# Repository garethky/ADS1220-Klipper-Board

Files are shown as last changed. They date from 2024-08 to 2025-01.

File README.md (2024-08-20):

# ADS1220-Klipper-Board
A board for connecting up to 4 Load cells to an ADS1220

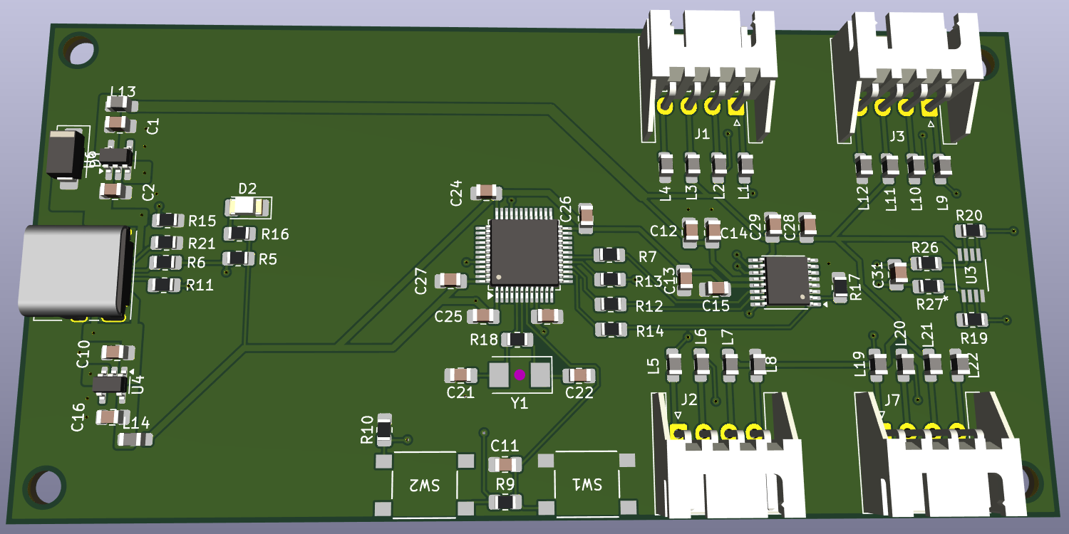
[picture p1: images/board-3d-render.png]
ADS1220 Board 3D Render


## Project Goals
This board is intended to be a reference design for eventual commercial boards that want to implement load cell probing.
We intend to tackle the following problems found with simple prototyping boards that connect via SPI I/O pins:

* Produce a clean 5V power supply on board for low noise load cell bridge measurements
* Reject common 3D printer electrical noise sources including: Voltage Regulators, Steppers, Heaters & 50Hz/60Hz line noise
* Gracefully handle Voltage Spikes & Ground Loops
* Provide Amplification/Gain to support low sensitivity (1mV/V) load cells to be able to measure 1g of force change
* Ability to connect up to 4 load cells in parallel to measure force on a printer's bed

Eventually we would like individuals to be able to order a board from a board house, once we nail down the component selection.

## Project Status: Prototyping
This is currently in the prototyping stage. Prototype goals are as follows:

1. Get it to work!
1. Prototype and test one 5V supply architecture (12V -> 5V via low noise switching regulator)
2. Test 5V to 3.3V via LDO
3. Test with and without 1 differential amplifier. 
4. Investigate voltage spikes and ground loops.

Future prototypes will refine the board:
1. Investigate additional 5V suppy architectures
2. Investigate additional amplifiers
2. Design for Supply Chain an Manufacturability: investigate component alternatives that are asier to get in the CN component supply chain.

## Specs
* ADC: [Texas Instruments ADS1220](https://www.ti.com/product/ADS1220)
* Additional differential amplifier: TK (prototype will try the [Microchip MCP6V92](https://www.microchip.com/en-us/product/mcp6v92) )
* * 4 x 4 pin JST HX connectors for full bridge load cells
* MCU: STMicro [STM32F103C8T](https://www.st.com/en/microcontrollers-microprocessors/stm32f103c8.html) MCU, Arm® Cortex® Cortex M4 @ 75Mhz
  * Klipper and Katapult support this chip well, including flashing over CAN if we decide to enable that later
* USB C for communicating with a klipper host
* Physical Boot and Reset buttons

## Why the ADS1220?
Several printers have shipped with the HX711 ADC chip which only supports 80 samples per second (SPS).
We consider this to be too slow for use as a Probe in the 3D printer as probing speed is limited to ~2mm/s.
There is a faster variant, the HX717, that supports 320 SPS. This shipped in all of Prusa's Nextuder products
and those support probing at up to 10mm/s. We consider this the minimum sample rate required for a 3D printer.

Both of these chips have the disadvantage of not being standard SPI devices and requiring a lot of MCU overhead to support communication.
Their data sheets are also lacking a lot of detail and the HX717 datasheet isnt available in English.

The ADS1220 is a good match for the capabilities of the HX717. Specifically:
* It supports faster sample rates close to 320SPS: 330, 350, 600, 660, 1000 & 1200. Higher sample rates improve the safety margin for
probing if the noise can be kept low and the sensitivity is high. Other ADC chips tend to have a large gap in the sample rate range from 
around 300SPS to 1000SPS.
* It has a PGA that supports up to a gain setting of 128
* Supports standard SPI
* TI provides a detailed datasheet and have reference designs
* Relatively cheap and widely available in the supply chain. Cost is a large
factor in getting a part into a commercial 3D printer board.

Features lacking on the ADS1220:
* The SPI speed is slow
* It lacks a "power reset" register. Reboots due to voltage spikes cant be detected at runtime.
The HX711 & HX717 also lack this feature. Higher end TI product do have this e.g. ADS1263. If we were
shipping a commercial product we would insist on this safety feature.

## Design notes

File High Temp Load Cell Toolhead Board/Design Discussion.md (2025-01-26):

## Concept
This is a 3D printer Toolead board intended to print in a "high temperature" exclosure. 80C is the target limit. This is hot for consumer pastics (Nylon, PA) but not hot for industrial plastics (PEEK & PEI - 90  to 140C). This should provide good conditions for printing the new PPA based filaments.

Because of the chamber temperature the 2 main parts that are most susceptible to heat are kept out of the chamber: the heater MOSFET and the stepper driver.

## Features

* 1 x 6 pin connector to bring in USB data, 12-24V power and your choice of fan voltage.
* 1 x 4 pin port for full bridge load cells using the ADS1220 ADC sensor
* 2 x 3 pin Fan ports with RPM monitoring (Heatbreak Cooler & Part Cooler). Max 2A power draw for the fans, limited by the input pin.
* 2 x 2 pin thermistor ports for Hot End (using PT1000 or NTC) and Heatbreak temperature monitoring
* On board NTC thermistor for board/ambient temperature monitoring
* 1 x 4 pin Neopixel/Dotstar port for illuminating the print are supplied with 5V/500mA for toolhead lighting
* On board power conversion from 12V to 5V and 3.3V using a buck converter module and two LDOs for ADC reference level DC power supply. (Does not reley on your 5V or 3.3V source being noise free)
* USB communication via wire pair in the main connector (no separate USB connector required)
* USBC Port for debugging, bench running and updates
* STM32 F103 Core M3 CPU @72Mhz
* Single wire debug (SWD) port for flashing the MCU with [Katapult](https://github.com/Arksine/katapult)
* Reset button
* MCU Boot indicator LED - also indicates USB full speed pull-up enabled
* Activity LEDs for both fans, 5V and 3.3V power
* DotStar Micro LED for indicating whatgever you want to users
* Molex CLIK-Mate connectors. Support up to 2A of current per pin and are much nicer to use vs JST alternatives.
* ESD protection (TVS diodes) on all I/O pins.
* Guard Ring for ESD protection and grounding to chassis

## References
You cant learn anything quickly without looking at the work of others. I specifically want to credit:
* [HUVUD](https://github.com/bondus/KlipperToolboard) - This is a toolhead board with an integrated stepper drive that fits on the back of a NEMA17 stepper motor. This has some incredibly tight packaging and routing in the PCB design. This particularly encouraged me to stop worrying about overlapping cortyards and just pack things closer together.
* [Prusa's Open Source](https://www.prusa3d.com/page/open-source-at-prusa-research_236812/) efforts and specifically the Love Board ([schematics](https://www.prusa3d.com/downloads/Electronics_drawings/MK4_electronics_schematics.zip)) - This is the first commercial open source board with a load cell ADC. It also pays particular attention to ESD supression and noise filtering which I found absent in other projects. The level of robustness they are achieving is worth our attention.
* The Voron project's [Klipper Expander](https://github.com/VoronDesign/Voron-Hardware/tree/master/Klipper_Expander) - this was useful for getting the Fan MOSFETs correct.
* [Tiny Fan Board](https://github.com/Gi7mo/TinyFan) - I was particularly interested in having RPM monitoring on the fan ports and this board implements that.
* Rick Heartly for this [video on grounding](https://www.youtube.com/live/ySuUZEjARPY) and PCB stackups. I'm using his preferred 4 layer stackup for this board and implementing his ideas on ground planes and via stitching.

## Detailed Design Topics
Everything, in no particular order...

### Optional USB Port
USB is used as the communications protocol. The USB D+ and D- wire pair must be twisted together to provide a good connection. A shielded twisted pair cable could also be used for these wires, so long as it can meet the requirements for continuous flexing and chamber temperatures.

I didnt see a comprelling reason to opt for CAN bus. It requires extra hardware on the host. The cable requirements for CAN are similar to USB. (remember we aret doing the super high speed version of USB)

A USBC port is included on the back side of the part and not intended to be used during normal opperation. It is included for bench running the part and performing firmware updates before it is installed into a printer. Inital flashing can be accomplished via the debug port, so this hardware isnt required. USB cabes are not rated for continous flexing conditions and high temperatures in a 3D printer. We usually build custom cables out of PTFE coated wire that can flex, resist abrasion and withstand the high temps.

The power supplied by the USB cable runs the MCU. A protection diode is incuded to stop power flowing back over the USB cable if the main power supply and the USB supple are connected at the same time. Due to voltage drop at the protection diode the 5V LDO wont see more like 4.5V and will either run in dropout mode or fail to start. If the 5V section of the board doesnt work under USB power this is OK as its just a debugging connector. If opperation is required for some test, just plug in the 24V/12V supply.

### Power
General Power Architecture:

5V USB Power |
             |
12V / 24V    --> Buck Converter --> 5.75V |--> Precision LDO --> 5V Digital
                                          |--> Precision LDO --> 5V Analog
                                          |--> Precision LDO |
3.3V Debug Power ------------------------------------------- --> 3.3V Digital

To get the most out of the ADS1220 ADC a very low noise 5V Analog reference is required. Typical LDOs are good for this but there is a more specialized class of LDO for measurment applications like this 24bit ADC. Thats what I am using here. These LDOs are voltage spcific so no external tuning resistors are required. They also have built-in reverse voltage protection so the debug port can power the board without the need for extra protection diodes.

* When using the SWD header, 3.3V power is injected directly into the 3.3V power bus
* When using the USB connector 5V power is fed into buck converter via a reverse current protection diode. The buck converter opperate din dropout mode and passes on the 5V to the LDOs. The 5V LODs will alos opperate in dropout mode.
* When bother USB and 24V are connected the protection diode stops 24V from backfeeding onto the USB power line.

#### LDO Selection

Features considered when selecting the LDO:
* Support 500mA of current output
* Fixed Voltage - eliminate external resistor netowork and saves space
* Reverse voltage protection - eliminate external diodes
* Low output voltage noise, less than 25μVRMS
* A package large enough to place by hand
* Low RθJA - Low junction-to-ambient thermal resistance

I've selected this part: TI [TPS7A21-Q1](https://www.ti.com/product/TPS7A21-Q1)

The last point about RθJA requires some math to validate. Basically this is the value that will end up limiting the current the device can supply when its inside a hot chamber at 80C.

```
SUPPLY_CURRENT = ((T(JUNCTION_MAX) – T(APPLICATION_TARGET)) / RθJA) / (V(SUPPLY) - V(OUTPUT))
```

For the TPS7A21-Q1, the T(JUNCTION_MAX) is 150°C, the RθJA of the VSON package is 58.9°C/W. The maximum input voltage to the LDO is 6V, but the target input voltage is 5.5V. Results with a value larger than the devices capacity of 500mA means there is some headroom.

```
3.3V Current @ 80°C = ((150°C - 80°C) / 58.9°C/W) / (5.5 - 3.3) = (1.19) / 2.7 = 540mA
5V Current @ 80°C   = ((150°C - 80°C) / 58.9°C/W) / (5.5 - 5.0) = (1.19) / 1.0 = 2376mA
```

If you run the calculations for a 100°C target chamber temp you still get results that are compleatly usable:

```
3.3V Current @ 100°C = ((150°C - 100°C) / 58.9°C/W) / (6.0 - 3.3) = (0.85) / 2.7 = 358mA (thermally limited!)
5V Current @ 100°C   = ((150°C - 100°C) / 58.9°C/W) / (6.0 - 5.0) = (0.85) / 1.0 = 1697mA
```

And the good news is the 5V LDO still has headroom and it is the one running the Neopixels which will pull the majority of the current from. The 3.3V rail shouldn't be pulling more than 200ma.

It is important to note that only the "DRB" 3mm x 3mm package has the good RθJA. The Specific part numbers are:

TPS7A2150PQWDRBRQ1 - 5V
TPS7A2133PQWDRBRQ1 - 3.3V

#### Buck Converter Selection
This components role is to steps down the voltage from 24V to 5.5V without generating lots of heat.

Features considered when selecting the Buck Converter:
* A Module with integrarated inductor - no hand layout required
* Support at least 1A of current output to drive both LDOs
* Support 12V-24V input voltage which are common primary supply voltages on 3D Printers
* A package large enough to hand assemble
* Low RθJA - Junction-to-ambient thermal resistance

The Buck converter is a module with a built in inductor. There is a whole art to using buck converters with external inductors. The routing of the traces can produce noise if not done correctly. A module sidesteps these concerns and reduces the complexity and part count. It just needs bulk capacitors and a resistor feedback network to opperate.

TI parts TPSM336x5 and TLVM236x5, which are the same architecture with different ranges of ouput voltage selection. Since the LDO's can accept no more than 6V, the [TLVM23615](https://www.ti.com/lit/ds/symlink/tlvm23615.pdf) is a good fit as it gives better resolution (more resistor choices) in voltage selection to 5.5V.

Thermal calculations for the buck convter are a bit different.
* T(JUNCTION_MAX) is 125°C
* Approximate efficiency is 87% or 0.87
* RθJA = 22°C/W

```
IOUT MAX = ((T(JUNCTION_MAX) – T(APPLICATION_TARGET) / RθJA) * (EFFICIENCY / 1 - EFFICIENCY) * (1 / VOUT)
```

Again, any result greater than the devices rated current of 1.5A is an indication of headroom:

```
IOUT MAX @ 80°C = ((125°C - 80°C / 22°C/W) * (0.87 / (1 - 0.87)) * (1 / 5.75) = 2.4 A
IOUT MAX @ 100°C = ((125°C - 100°C) / 22°C/W) * (0.87 / (1 - 0.87)) * (1 / 5.75) =  1.3 A (thermally limited!)
```

The module is not thermally limited at the target temp of 80C and has enough headroom to meet the applicaiton requirements at 100C.

#### Buck Converter Resistor Selection
TLVM23615 uses a resistor divider to set the output voltage between 1V and 6V. The LDO's require some margin above 5V for dropout and for voltage sags so a target of 5.5V was selected. The two resistors are called RFBB and RFBT. RFBB is typically 10kΩ and RFBT is calculated as:

RFBT kΩ = RFBB kΩ × (VOUT - 1)
RFBT kΩ = 10kΩ × (5.5 - 1) = 45kΩ

Unfortunatly, 45kΩ isn't a common size. But 45.3kΩ is. So what voltage will that yield:
45.3kΩ = 10kΩ × (VOUT - 1)
(45.3kΩ / 10kΩ) = VOUT - 1
(45.3kΩ / 10kΩ) + 1 = VOUT
VOUT = 5.53V

This is prefectly acceptable.

### PCB Stackup
The PCB stackup is: Ground/Components, Signal/Ground, Power/Signal/Ground, Ground/Components

OSH Park's 6 layer board is 'built different'. They have one large core in the middle with samller 4mil cores in between the top 3 and bottom 3 layers. This is in contrast to other stackups where its 3 double sided sheets with 2 cores.
```
1) ---Sig/PWR---
2) ---GND---
3) ---Sig/PWR---
   ===Core=== (36mil)
4) ---Sig/GND---
5) ---GND---
6) ---Sig/GND---
```
With this stackup, layers 1 and 3 reference the ground plane on 2. A signal routed on 1 and 3 doesnt require a ground return via because the ground plane doesnt change. Signals on 4 and 6 reference ground on 5. Signals moving from those layers to/from components on 1 need a ground via as a return path next to the signal via.

Because of the large core, there in minimal interaction between layers 3 and 4. But putting power on layer 4 provides a reference plane fore layer 3, in addition to the pure ground plane on layer 2.

The LDO's and Buck Converter get their best thermal performance when the board has as much copper in it as possible. Basically its a large heat spreader. Since the plan is already to pour ground everywhere this fits perfectly with what the VRMs want.

### Guard Ring
The bord is circled by a guard ring that is 2mm wide, placed on every layer of the board and stitched together with vias. The copper is exposed to allow it to be condutive. The mounting holes and mounting points on the external connectors are all tied into the guard ring.

A spot for a TVS diode to bridge the guard ring to the ground plane is provided but at the time of design its not clear if this is the right thing to do. Other options exist:
* GND and the guard ring can be connected with a large resistor.
* The guard ring can be left floating to pass ESD spikes around the board and back into the printers frame via the mounting holes.
* The load cell can be grounded to the guard ring by attacing a ring terminal to a ground wire and fixing it to the adjacent mounting point.
* The guard ring can be connected back to chassis ground via a dedicated wire back to the electronics bay. Again this can be done with ring terminals.
* ESD transmissable plastic could be used to create a cover for the board that would then be electrically connected to the guard ring.

The aim of the prototype is to test these options out in a real printer to see what performs best.

### Via Stitching
Ground planes and the Guard Ring have via stitching applied.

### ESD Protection
ESD protection, we should have some... ESD protection devices on digital lines seems to be industry standard practice and Prusa's design does this as well.

Large TVS diode between the main 24V supply and the ground plane to stop power entry ESD.

Unidirectional 3.3v TVS diodes on:
  * ADC input line for the Heatbreak Thermistor
  * ADC input lines for the Fan RPM
  * ADC input for the filament sensor (filament sesnor can be on/off or use an ADC value)

Bi-direction 3.3V TVS diodes on:
  * USB Pair

Unidirectional 5v TVS diodes on:
  * LED clock and data output line

### High Frequency Noise Filtering
Sensitive components are guarded with Ferrite beads (120R@100Mhz/3A) to filter high frequency noise.
* Load Cell lines
* Filament sensor power lines
* PT100 port lines
* Heatbreak thermistor lines
* LED power lines

### Trace Widths
The board isnt "Controlled Impedance" but I'm using the trace widths from the data table from the board house: [6 Layer impedance table](https://docs.oshpark.com/resources/six-layer-impedence-table.png).

I added the trace widths and some custom design rules to route traces by netclass at the appropriate width on outer and inner layers.

### Via Sizing
The default KiCad via size of 0.3mm / 0.6mm have an ampacity of over 2A. Thats good for basically everything on the board. The board house cant go much smaller than this anyway. In some places around the MCU i have used a smaller via size to help make space for the fanout.

### Capacitor Sizes
Capacitors de-rate at the target 80C chamber temperatures. Larger capacitors de-rate less than smaller ones. I'm also hand assembling the board and decided the smallest component I want to place manually is a 0603. This chart is used to select capacitor sizing:

| Range C | SMD Size | Type | Voltage | Range |
|---|---|---|---|---|
| 1pf - 10nf | 0603 | Ceramic C0G | 25V | 10% |
| 10nf - 0.1uf | 0603 | Ceramic X7R | 25V | 10% |
| 0.1uf - 2.2uF | 0805 | Ceramic X7R | 25V | 10% |
| 2.2uF - 22uF | 1206 | Ceramic X7R | 70V | 10% |

Nothing in the design requires an electrolytic capacitor.

### LEDs
Leds are driven by 24V, 5V and 3.3V power. Resistors are selected to limit the LED's driven current to about than 2ma. 3.3V output pins on the MCU supply a maximum of 25mA of current.

[LIST-C193KRKT-5A - LiteOn](https://optoelectronics.liteon.com/upload/download/DS22-2005-077/LTST-C193KRKT-5A.PDF)
Forward Voltage: 2.0V
Forward Current: 1.5mA

| LED Module | Supply Voltage | Resistor | Current | Forward Voltage (FV) |
|---|---|---|---|---|
| LIST-C193KRKT-5A | 24V  | 10KΩ | 2.2mA | 2.0v |
| LIST-C193KRKT-5A | 5V | 2kΩ | 1.5mA | 2.0v |
| LIST-C193KRKT-5A | 3.3V | 1kΩ | 1.3mA | 2.0v |

Resistors should be able to handle 1/2 watt of power or better. Usually this requires 0805 size resistors.

Some tuning of this might be required in the prototype based on brightness.

### Fans

#### Fan Voltage
A dedicated input pin allows you to pick the supply voltage for the fans. I dont have to generate 12V on board to run them.

#### Fan RPM Monitoring
My personal view is that cooling fans are safety critical systems that should be monitored. If the fan fails the printer should shut down the heater. So the fans on this board feature an RPM monitoring pin. There are plenty of fans in the supply chain that have this feature.

#### No Fan PWM Output
4 Wire fans in this size do exist but they are very rare. If you use a 4 wire fan, you dont need to put MOSFETs on the board to drive the fans. This effectivly means you can get the MOSFET into the place where its more likely to get cooled. But the lack of fans means this is very unlikely to happen, so I left this out. If I had my way I would require 4 wire fans and omit the MOSFETs.

#### Tach Line Resistor
Fans report their RPM or Tachometer as a square wave. A reference voltage is supplied in to the fan's tachometer input. The fan then pulls this line low to create a square wave. This means the tach line voltage supply connects to ground inside the fan. Both [Noctua](https://noctua.at/pub/media/wysiwyg/Noctua_PWM_specifications_white_paper.pdf) and [Sunon](https://www.sunon.com/PROSEARCH_FILES/(D04115420G-01)-1.pdf) require limiting the current flowing through the tach line to not more thean 5mA. This is important to do as, when the RPM is 0, the line may be pulled low continouously causing a large current flow through the fan. All the other designs I have seen omit this resistor.

E.g. the [Tiny Fan Board](https://github.com/Gi7mo/TinyFan) uses an in-mcu pull-up on the ADC line and connects it directly to the Tachometer input. The Pins on an STM32 chip can supply up to 25mA which is 5x higher than the industry spec.

```
R = V/I
R = 3.3V / 5mA
R = 660 Ohm
```

This is really close to 1k, so thats what im using as this helps with BOM consolidation.

#### Fan MOSFET Selection
Slection criteria:

* The max voltage is 24V. So at least a 30V (Drain to Source V<sub>DS</sub)) device is required.
* Duty cycle is 100% / full DC on. We do use PWM for the part cooling fan but the hot end fan is usually 100% on.
* Ambiend temp target is 80C.
* The gate drive voltage is 5.0. So V<sub>GS</sub> needs to be less than 3.3V. I'm re-using the level shifter part to step up the 3.3V GPIO voltage to 5V.
* Because of the focus on 100% duty cycle we want a very low resistance MOSFET. Leakage current isnt really an issue in this application.
* The current required is less than 1A. However it has to do this at 100% duty cycle at 80C ambient.

The last part is actually really difficult. Most data sheets show 100% duty cycle under ideal conditions, both gate drive voltage and ambient temperature. We will have neither of these conditions.

I didnt want to conduct a survey of all possible MOSFET parts, so I looked in TI's parts bin and found: [CSD17581Q3A](https://www.ti.com/lit/ds/symlink/csd17581q3a.pdf)

I increased the gate resistor value from 100 Ohms to 1K Ohms. Some designs omit this resistor, but this increases power used by the MOSFET and drives up its temperature. I'd like to have some math to work out the how fast the gate needs to switch and calulate an optimal value. Klipper's default switching time is 10ms in software PWM mode. This is 100Hz, a very slow switching speed. It is possible that higher switching speed might work for some fans when using hardware PWM.

#### Fans and N-Channel MOSFETs
An N channel mosfet switches the ground lead of the fan. This disconnects the fan from ground. This should also defeat the fans ability to pull the Tach line low, disrupting the tach signal. For a safety monitoring usecase, this is an acceptable defect. We dont need the reported RPM to be acurate.

This behaviour is something that I plan to investigate with a scope. I saw some suggestions that the ground lead should bypass the MOSFET with a high value pulldown resistor. I added these as do-not-populate parts on the board to experiment with.

### MCU Crystal

#### Why not an Oscillator Module?
I wanted to use a crystal oscillator module for this project to save on space and complexity. But I found this to be impossible with the current katapult/klipper codebase:

###### OSC_OUT Pin
This is the pin that would normally complete the crystal oscillator circuit. When using an oscillator module its less than clear what must be done from the documentation. But as best as I understand it:
* [AN1709](https://www.st.com/resource/en/application_note/an1709-emc-design-guide-for-stm8-stm32-and-legacy-mcus-stmicroelectronics.pdf) has an explicit diagram with the pin tied to ground when using an external clock source. This fits with the recommendation to tie all unued GPIO pins to GND to minimize noise.
* [AN5286](https://www.st.com/resource/en/application_note/an2586-getting-started-with-stm32f10xxx-hardware-development-stmicroelectronics.pdf) has a similar diagram (Figure 6) that shows the OSC_OUT pin unconnected with a "Hi-Z" note. Hi-Z mean high impedance. There is a "BYPASS" / `HSEBYP` mode that needs to be configured in software that disconnects the OSC_OUTPUT from the clock source. I assume this is how you set the "Hi-Z" mode for the pin.
* I'm pretty sure [this code](https://github.com/Arksine/katapult/blob/25a23cd420d7f0f7b677f1511b5739385fca72d9/lib/stm32f1/system_stm32f1xx.c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) in katapult turns off that bypass mode. This isn't user configurable, so the bypass mode is never available, meaning only crystals should be used.

Its not clear if using the module in non-bypass mode will work correctly if the pin is grounded or floating, since the bypass mode is not engaged.

#### Crystal Capacitor Selection

I selected [ECS-.327-6-34QCS-TR](https://ecsxtal.com/store/pdf/ECX-34Q.pdf) using the STM32 crystal selection tools. I wanted one that had a small footprint and a high temperature rating, this one is good to 125C.

The load capacitance of the crystal is 12.5pF. The 'back of the envelope' method for selecting a capacitor size is to double the load capacitance. So 25pF.

You can do the complete math. But STM's own document, [AN2867](https://www.st.com/resource/en/application_note/an2867-guidelines-for-oscillator-design-on-stm8afals-and-stm32-mcusmpus-stmicroelectronics.pdf), says the best thing to do is to measure the frequency generated with a scope and tune the capacitance based on those results. I'm not sure that my scope is good enough to do this.

### Unused Pins
What is the correct thing to do with unused pins?

STM have an app note [AN4899](https://www.st.com/content/ccc/resource/technical/document/application_note/group0/13/c0/f6/6c/29/3b/47/b3/DM00315319/files/DM00315319.pdf/jcr:content/translations/e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) that advises connecting all unused pins to GND: "If the application is sensitive to ESD, prefer a connection to ground".

There is however a risk specific to klipper with this. Klipper users can enable a pull-up on one of these pins by accident, creating a short to ground. This will probably cause that pin to burn out but it could do damage to other parts of the MCU in the process. The alternative is to use a resistor in the ground path to prevent this damage. This adds about 5 extra resistors around the MCU, which is space id rather not use up.

So the mitigation I have is to ship a klipper "pins file" which gives friendly names to all of the pins. This should discourage myself or someone else from doing a pull-up on the wrong pin. It also helps that NOTHING on the board requires a pull-up. All pull-ups have been done for you in hardware.

Most of the other chips have something similar in the documentation about connecting unused pins to ground.

### Test Points
Most of the items on the board can be gotten to via the rather generous pads for the connectors. Here is a list of everythign I want to scope and how im planning to get to it:

* GND - Via Connector Pad
* 3.3V - Test Point
* 5V Digital - TestPoint
* 5V Analog - TestPoint +  a local GND test point

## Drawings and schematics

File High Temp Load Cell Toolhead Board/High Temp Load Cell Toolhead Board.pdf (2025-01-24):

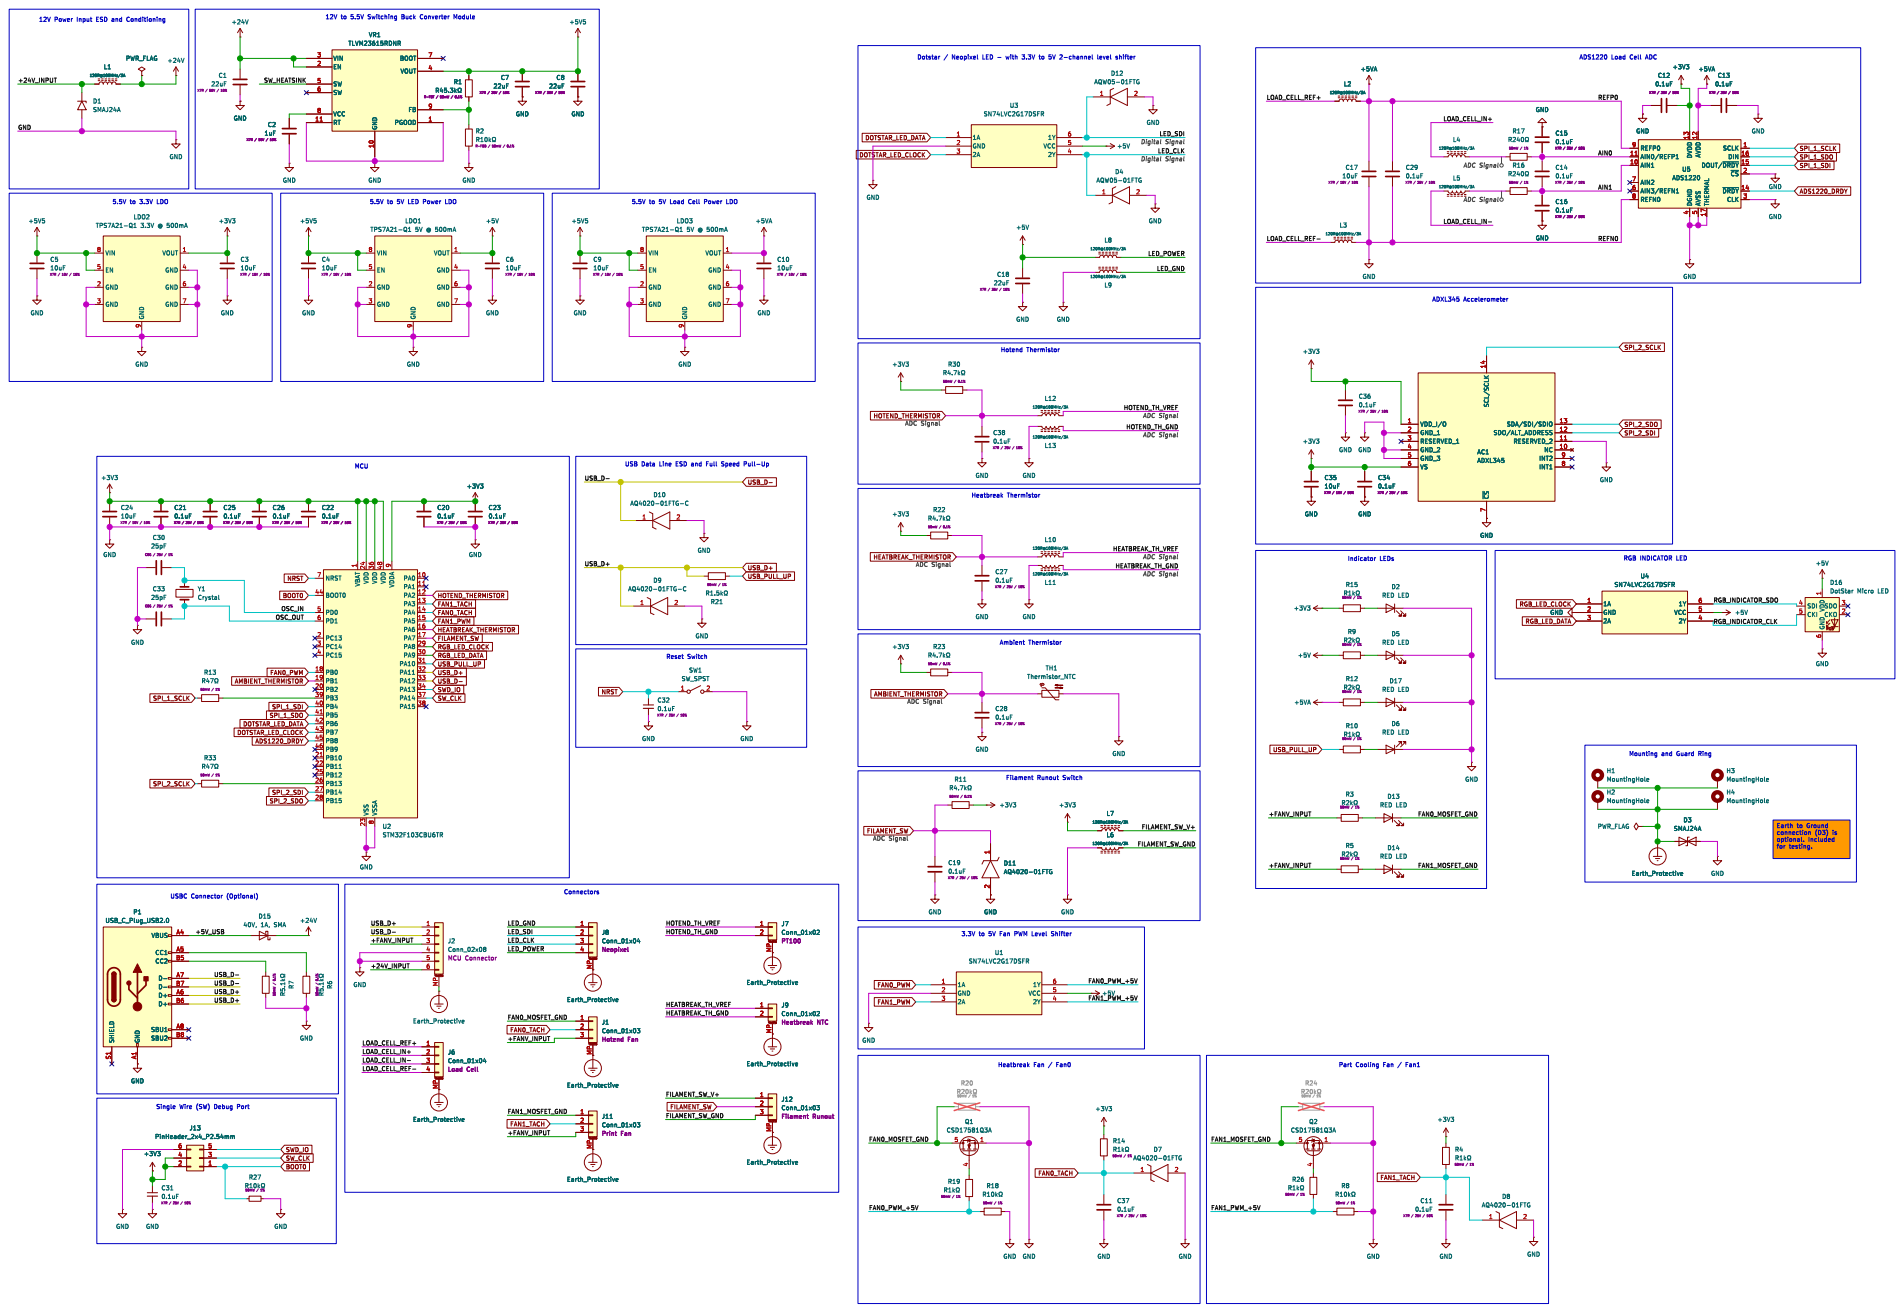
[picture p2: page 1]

12V Power Input ESD and Conditioning

16 THERMAL 17
~{DRDY} 14 DOUT/~{DRDY}15 DIN

SCLK

ADC Signal

ADXL345 Accelerometer 5.5V to 5V LED Power LDO

5.5V to 5V Load Cell Power LDO

1 PA0 10 PA1 11 PA2 12 PA3 13 PA4 14 PA5 15 PA6 16 PA7 17 PB0 18 PB1 19 PC13 2 PB2 20 PB10 21 PB11 22 VSS 23 VDD 24 PB12 25 PB13 26 PB14 27 PB15 28 PA8 29 PC14 3 PA9 30 PA10 31 PA11 32 PA12 33 PA13 34 VDD 36 PA14 37 PA15 38 PB3 39 PC15 4 PB4 40 PB5 41 PB6 42 PB7 43 BOOT0 44 PB8 45 PB9 46 VDD 48 PD0 5 PD1 6 NRST 7 VSSA

Single Wire (SW) Debug Port

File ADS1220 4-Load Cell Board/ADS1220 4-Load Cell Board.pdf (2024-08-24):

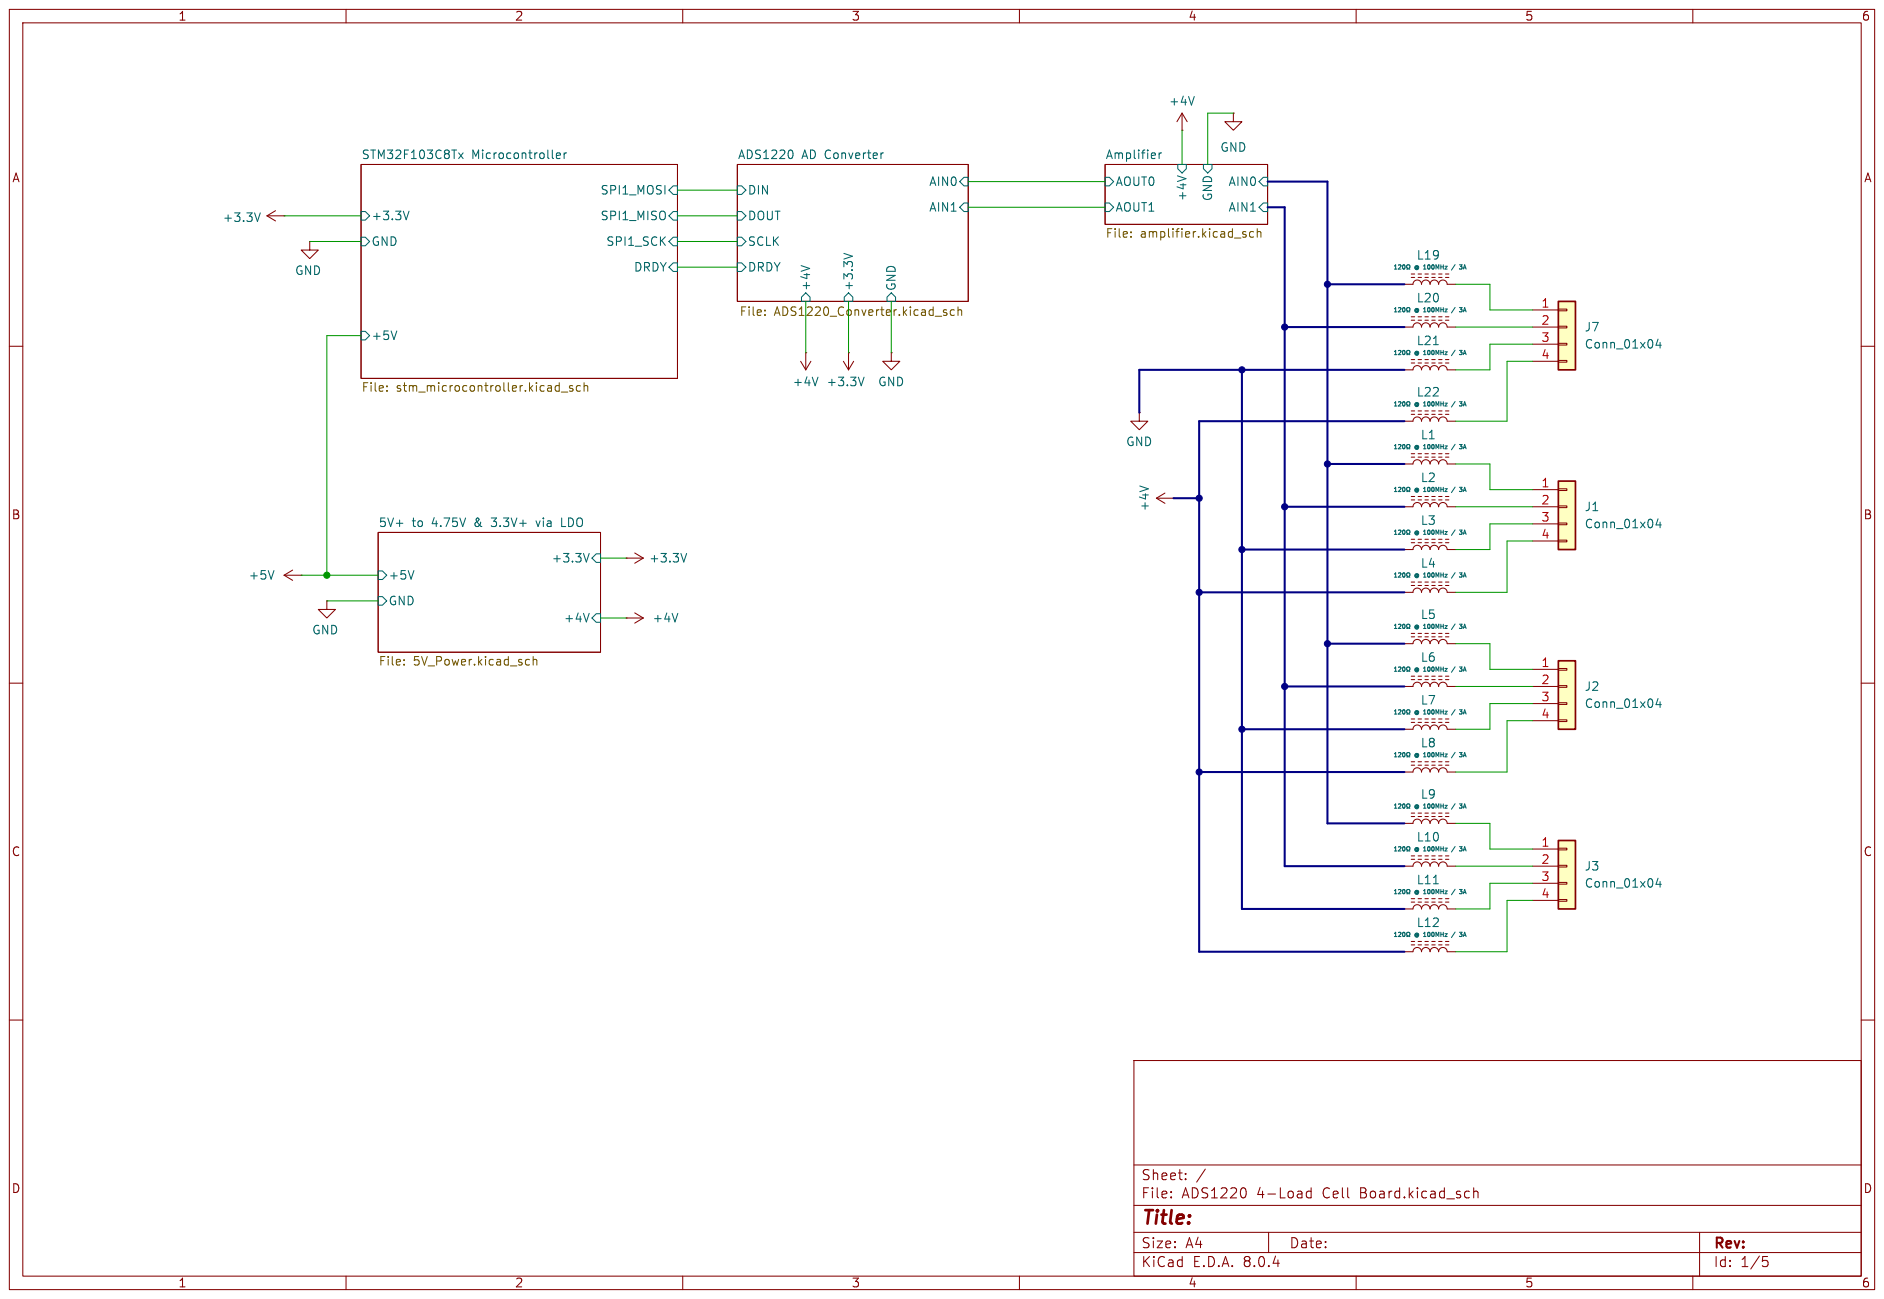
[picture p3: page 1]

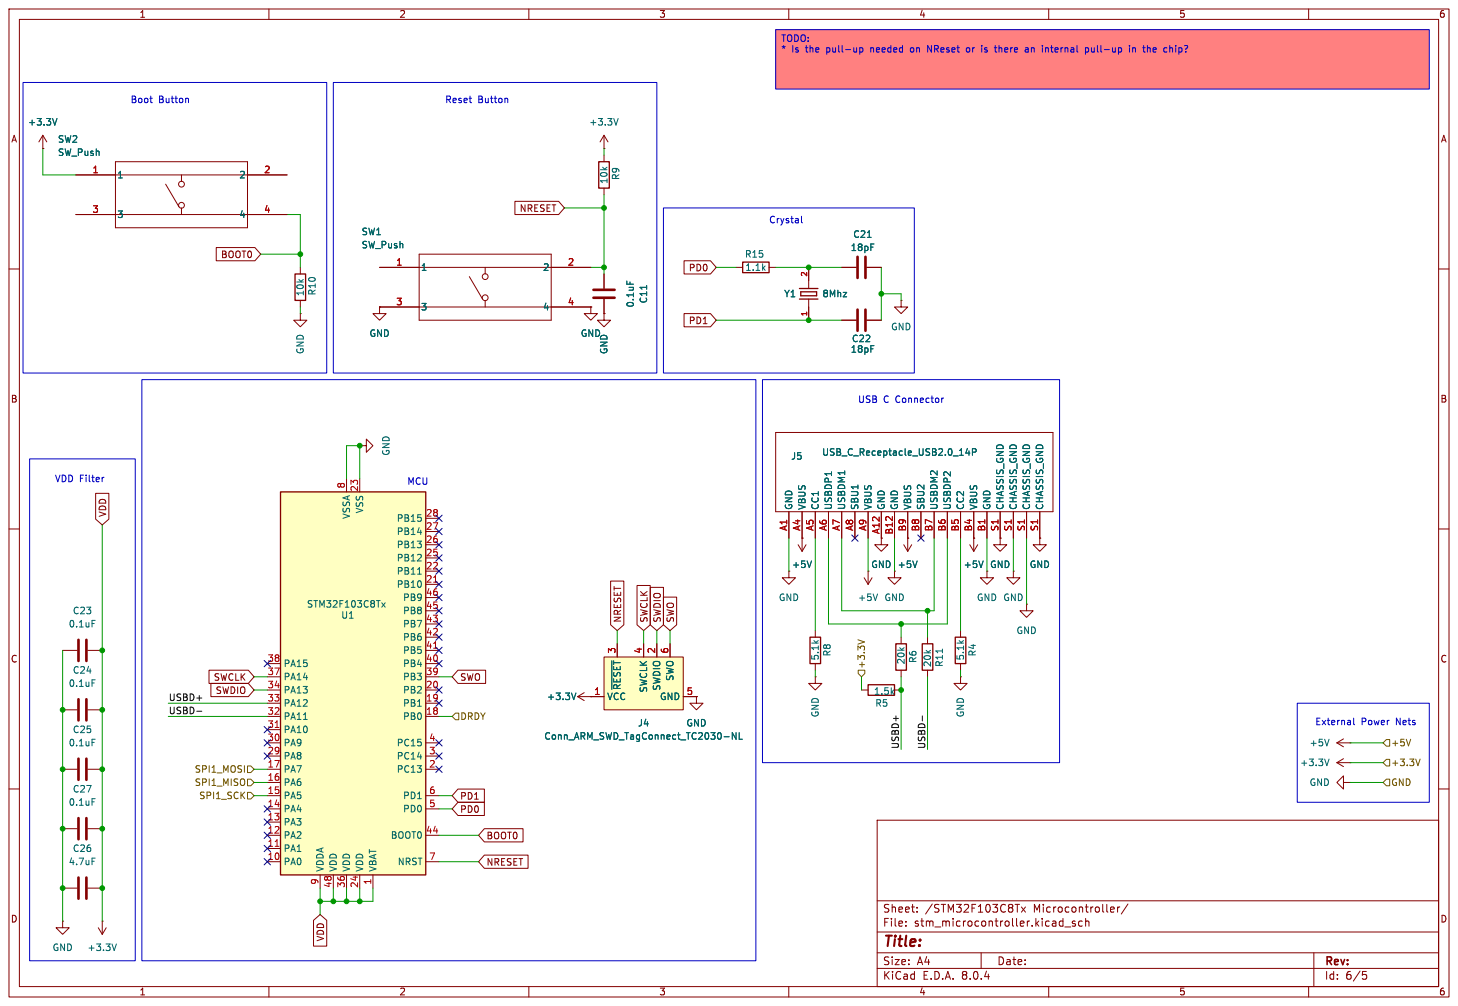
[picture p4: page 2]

1 PA0 10 PA1 11 PA2 12 PA3 13 PA4 14 PA5 15 PA6 16 PA7 17 PB0 18 PB1 19 PC13 2 PB2 20 PB10 21 PB11 22 VSS 23 VDD 24 PB12 25 PB13 26 PB14 27 PB15 28 PA8 29 PC14 3 PA9 30 PA10 31 PA11 32 PA12 33 PA13 34 VDD 36 PA14 37 PA15 38 PB3 39 PC15 4 PB4 40 PB5 41 PB6 42 PB7 43 BOOT0 44 PB8 45 PB9 46 VDD 48 PD0 5 PD1 6 NRST 7 VSSA

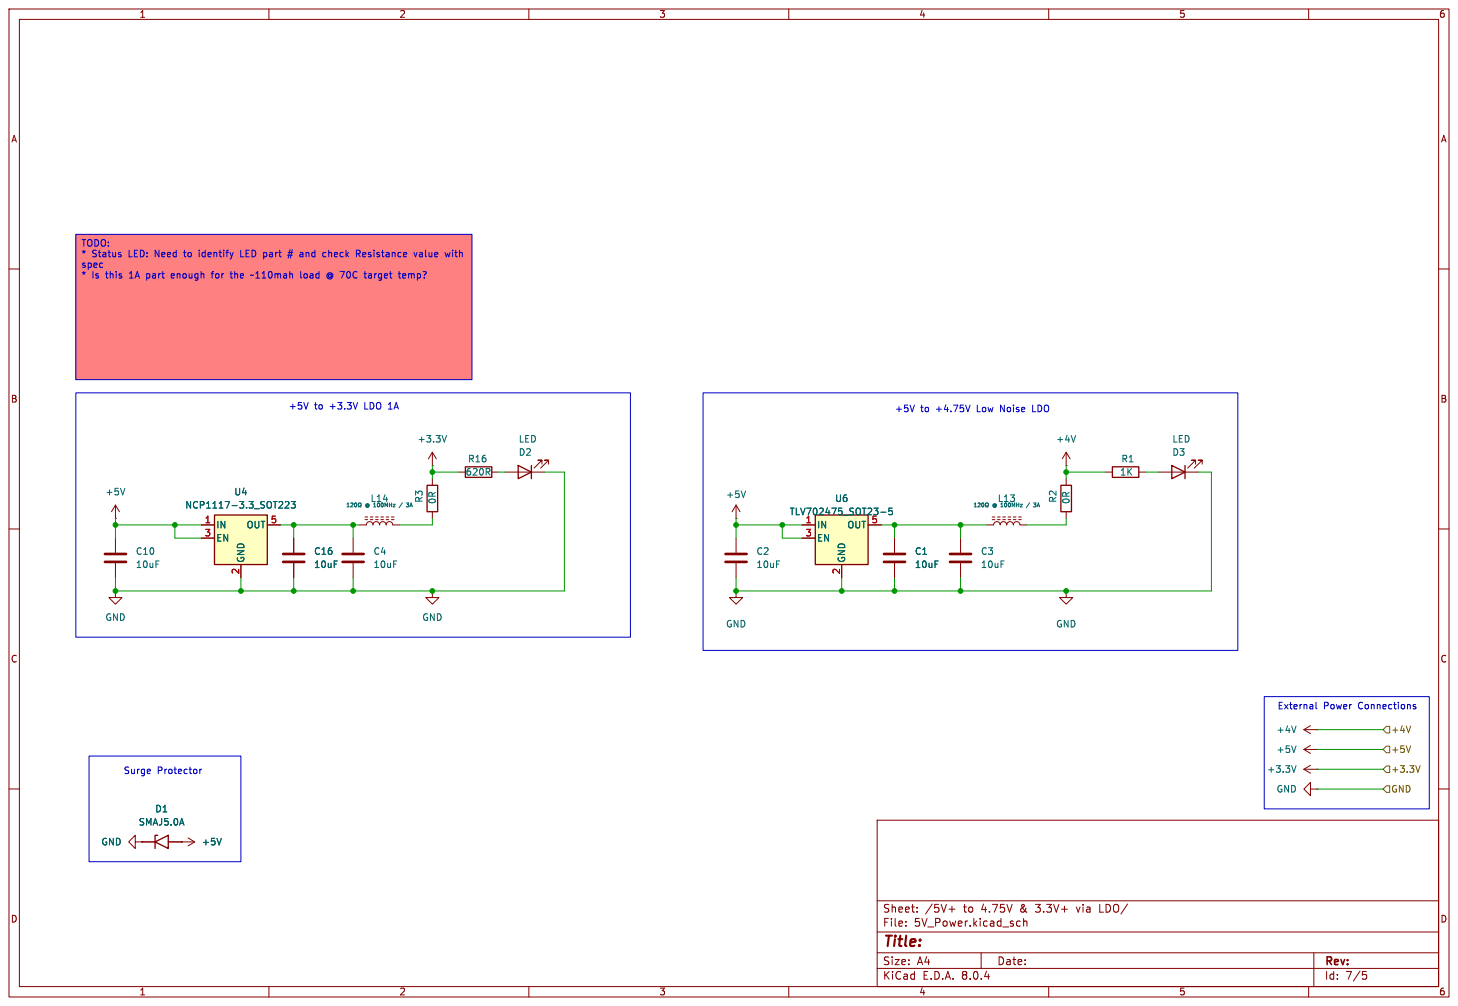
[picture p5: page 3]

spec
* Is this 1A part enough for the ~110mah load @ 70C target temp? C16

External Power Connections Surge Protector

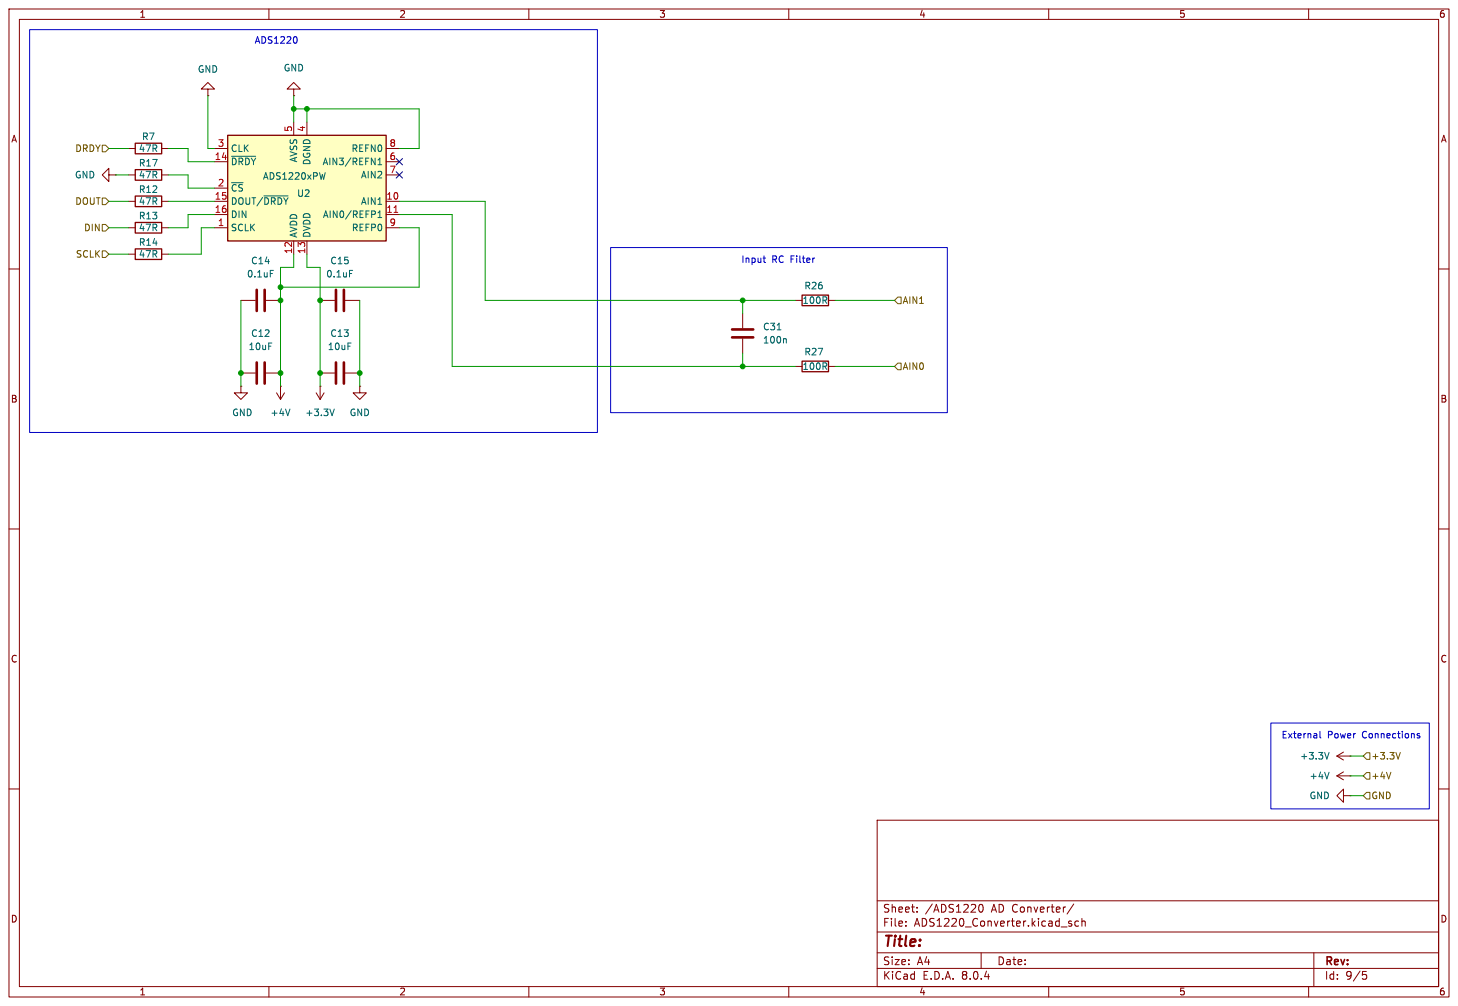
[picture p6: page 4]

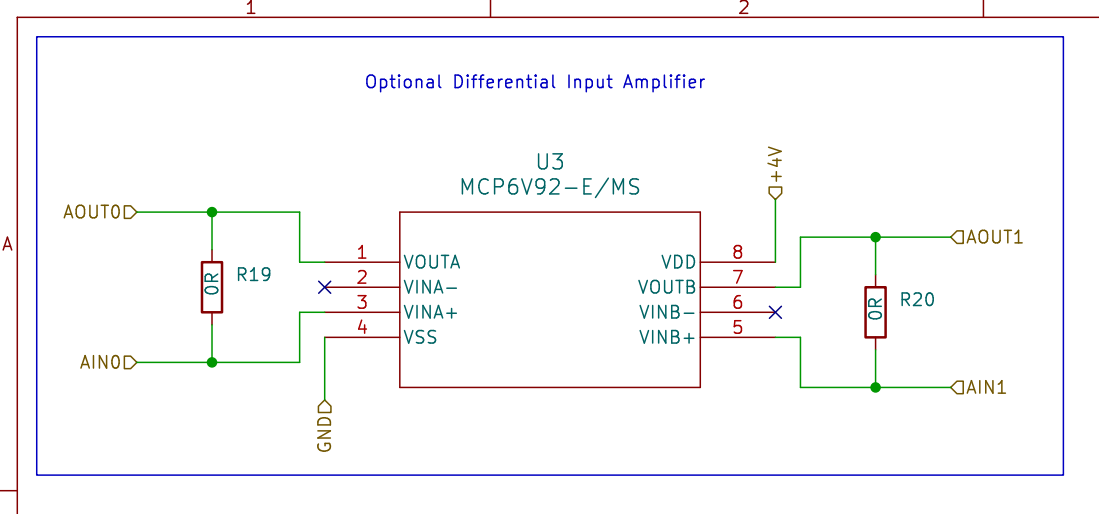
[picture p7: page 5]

Id: 10/5 Title: File: amplifier.kicad_sch Sheet: /Amplifier/

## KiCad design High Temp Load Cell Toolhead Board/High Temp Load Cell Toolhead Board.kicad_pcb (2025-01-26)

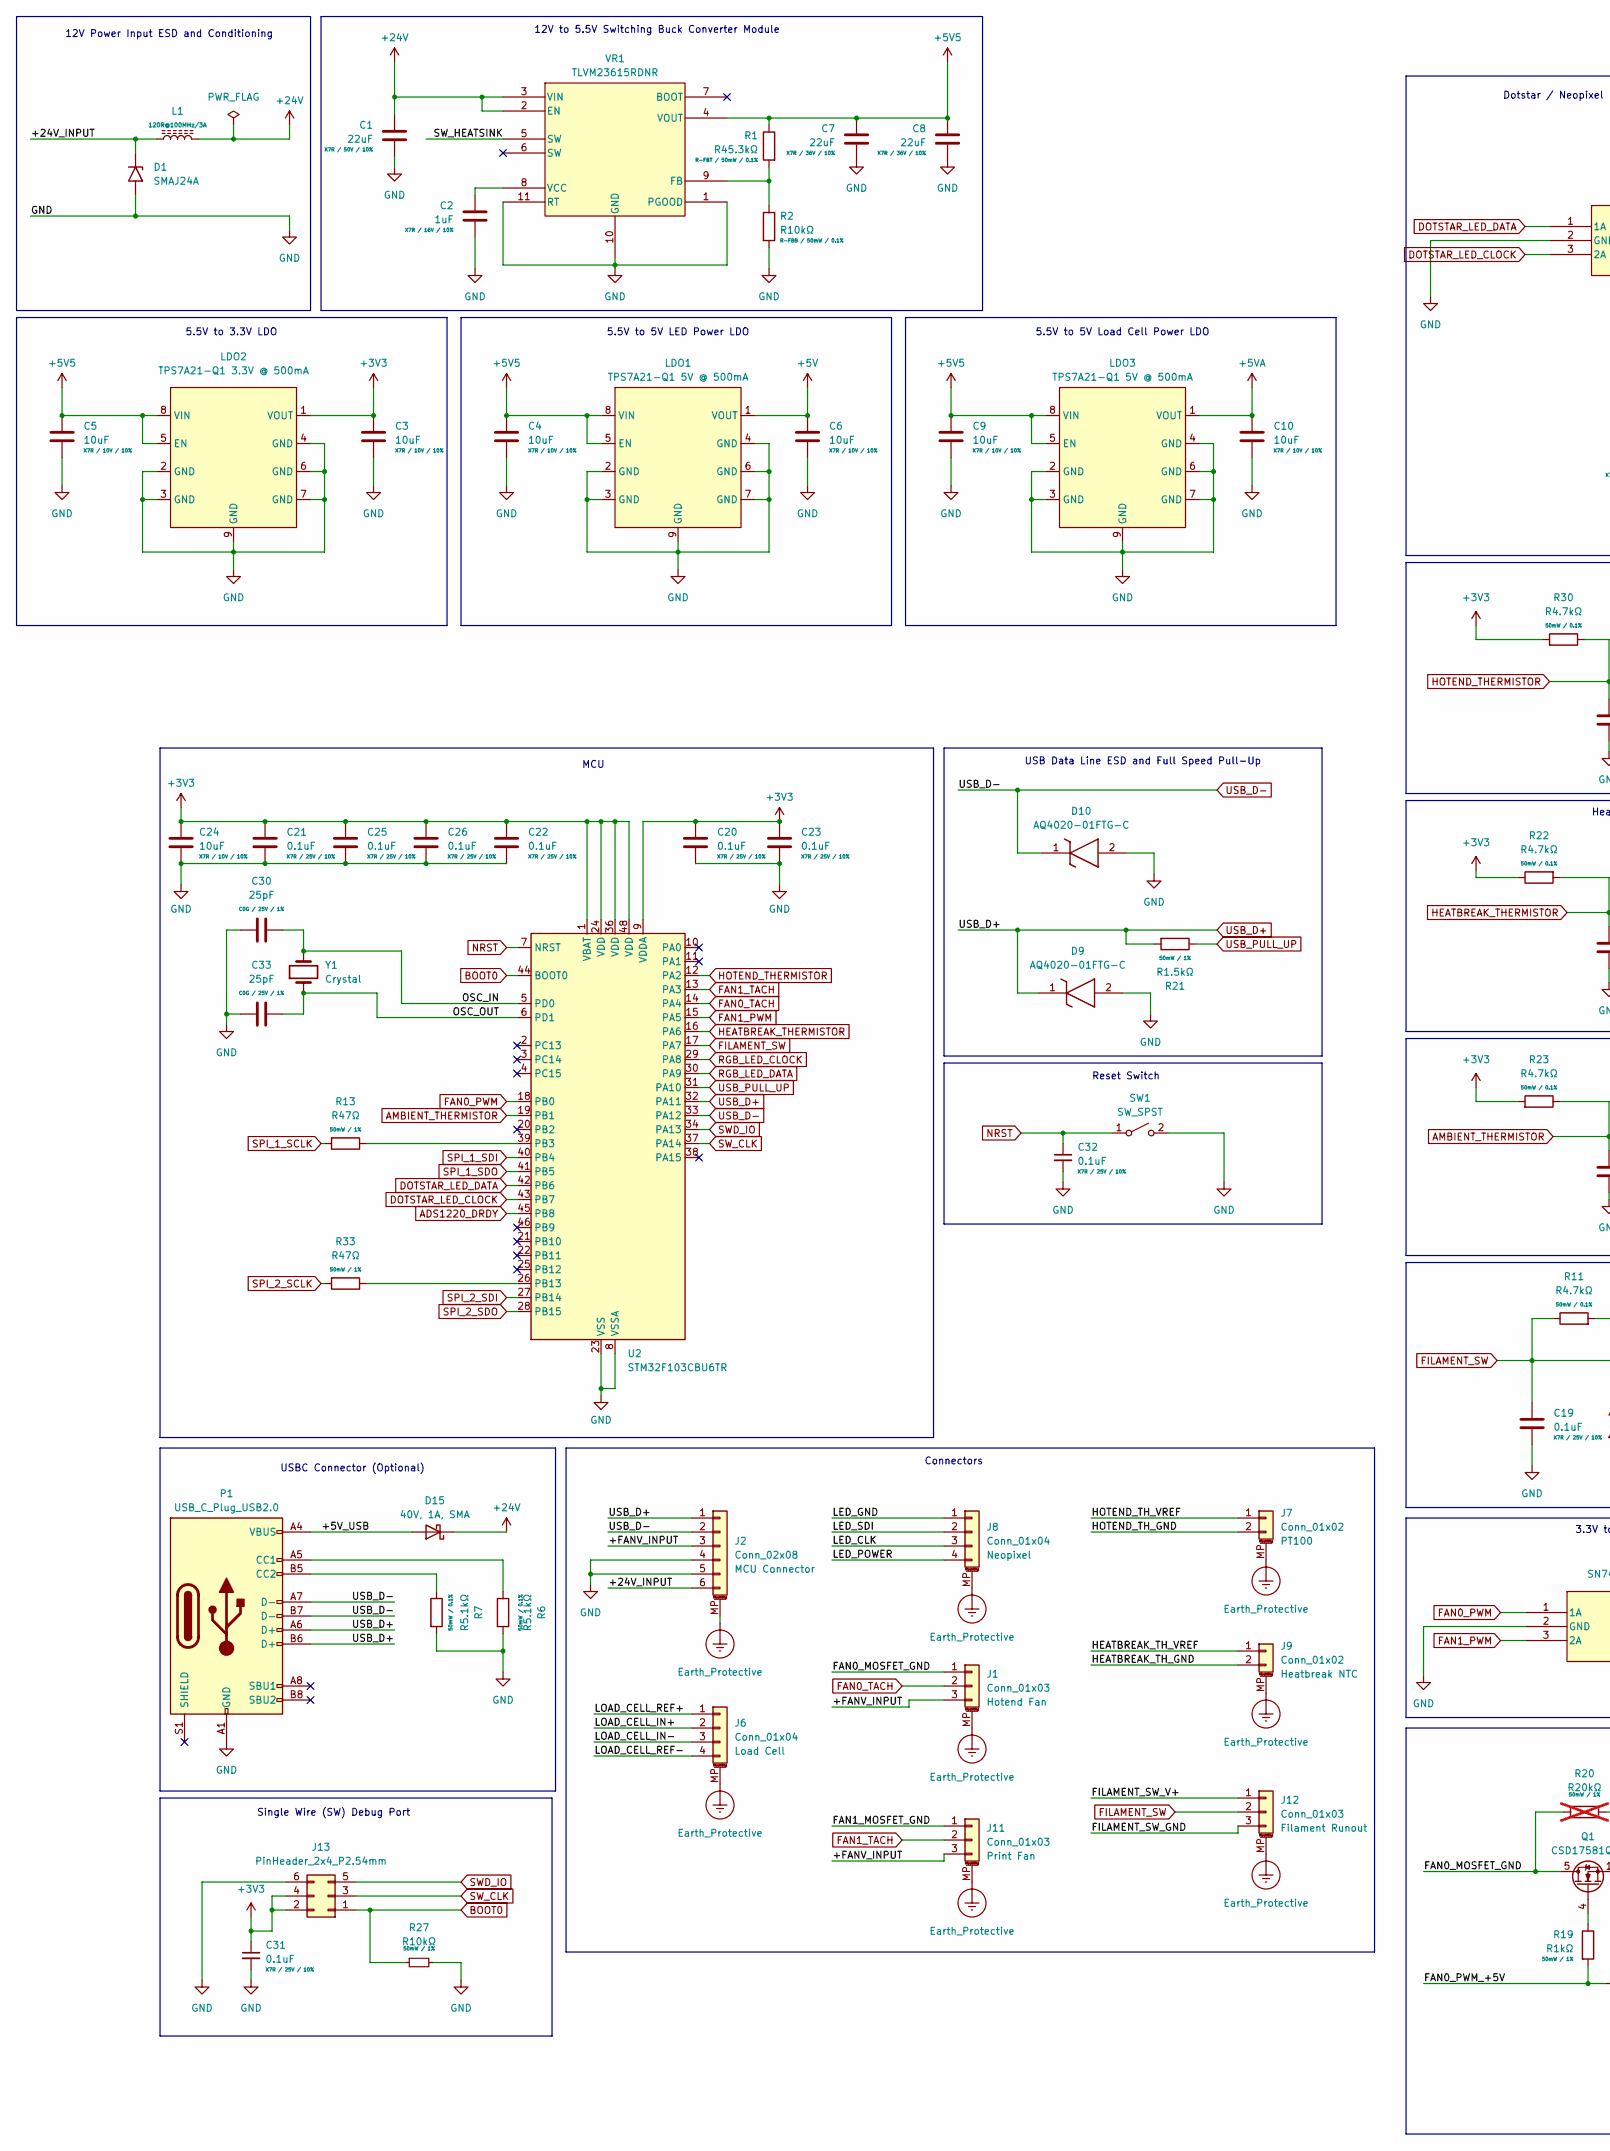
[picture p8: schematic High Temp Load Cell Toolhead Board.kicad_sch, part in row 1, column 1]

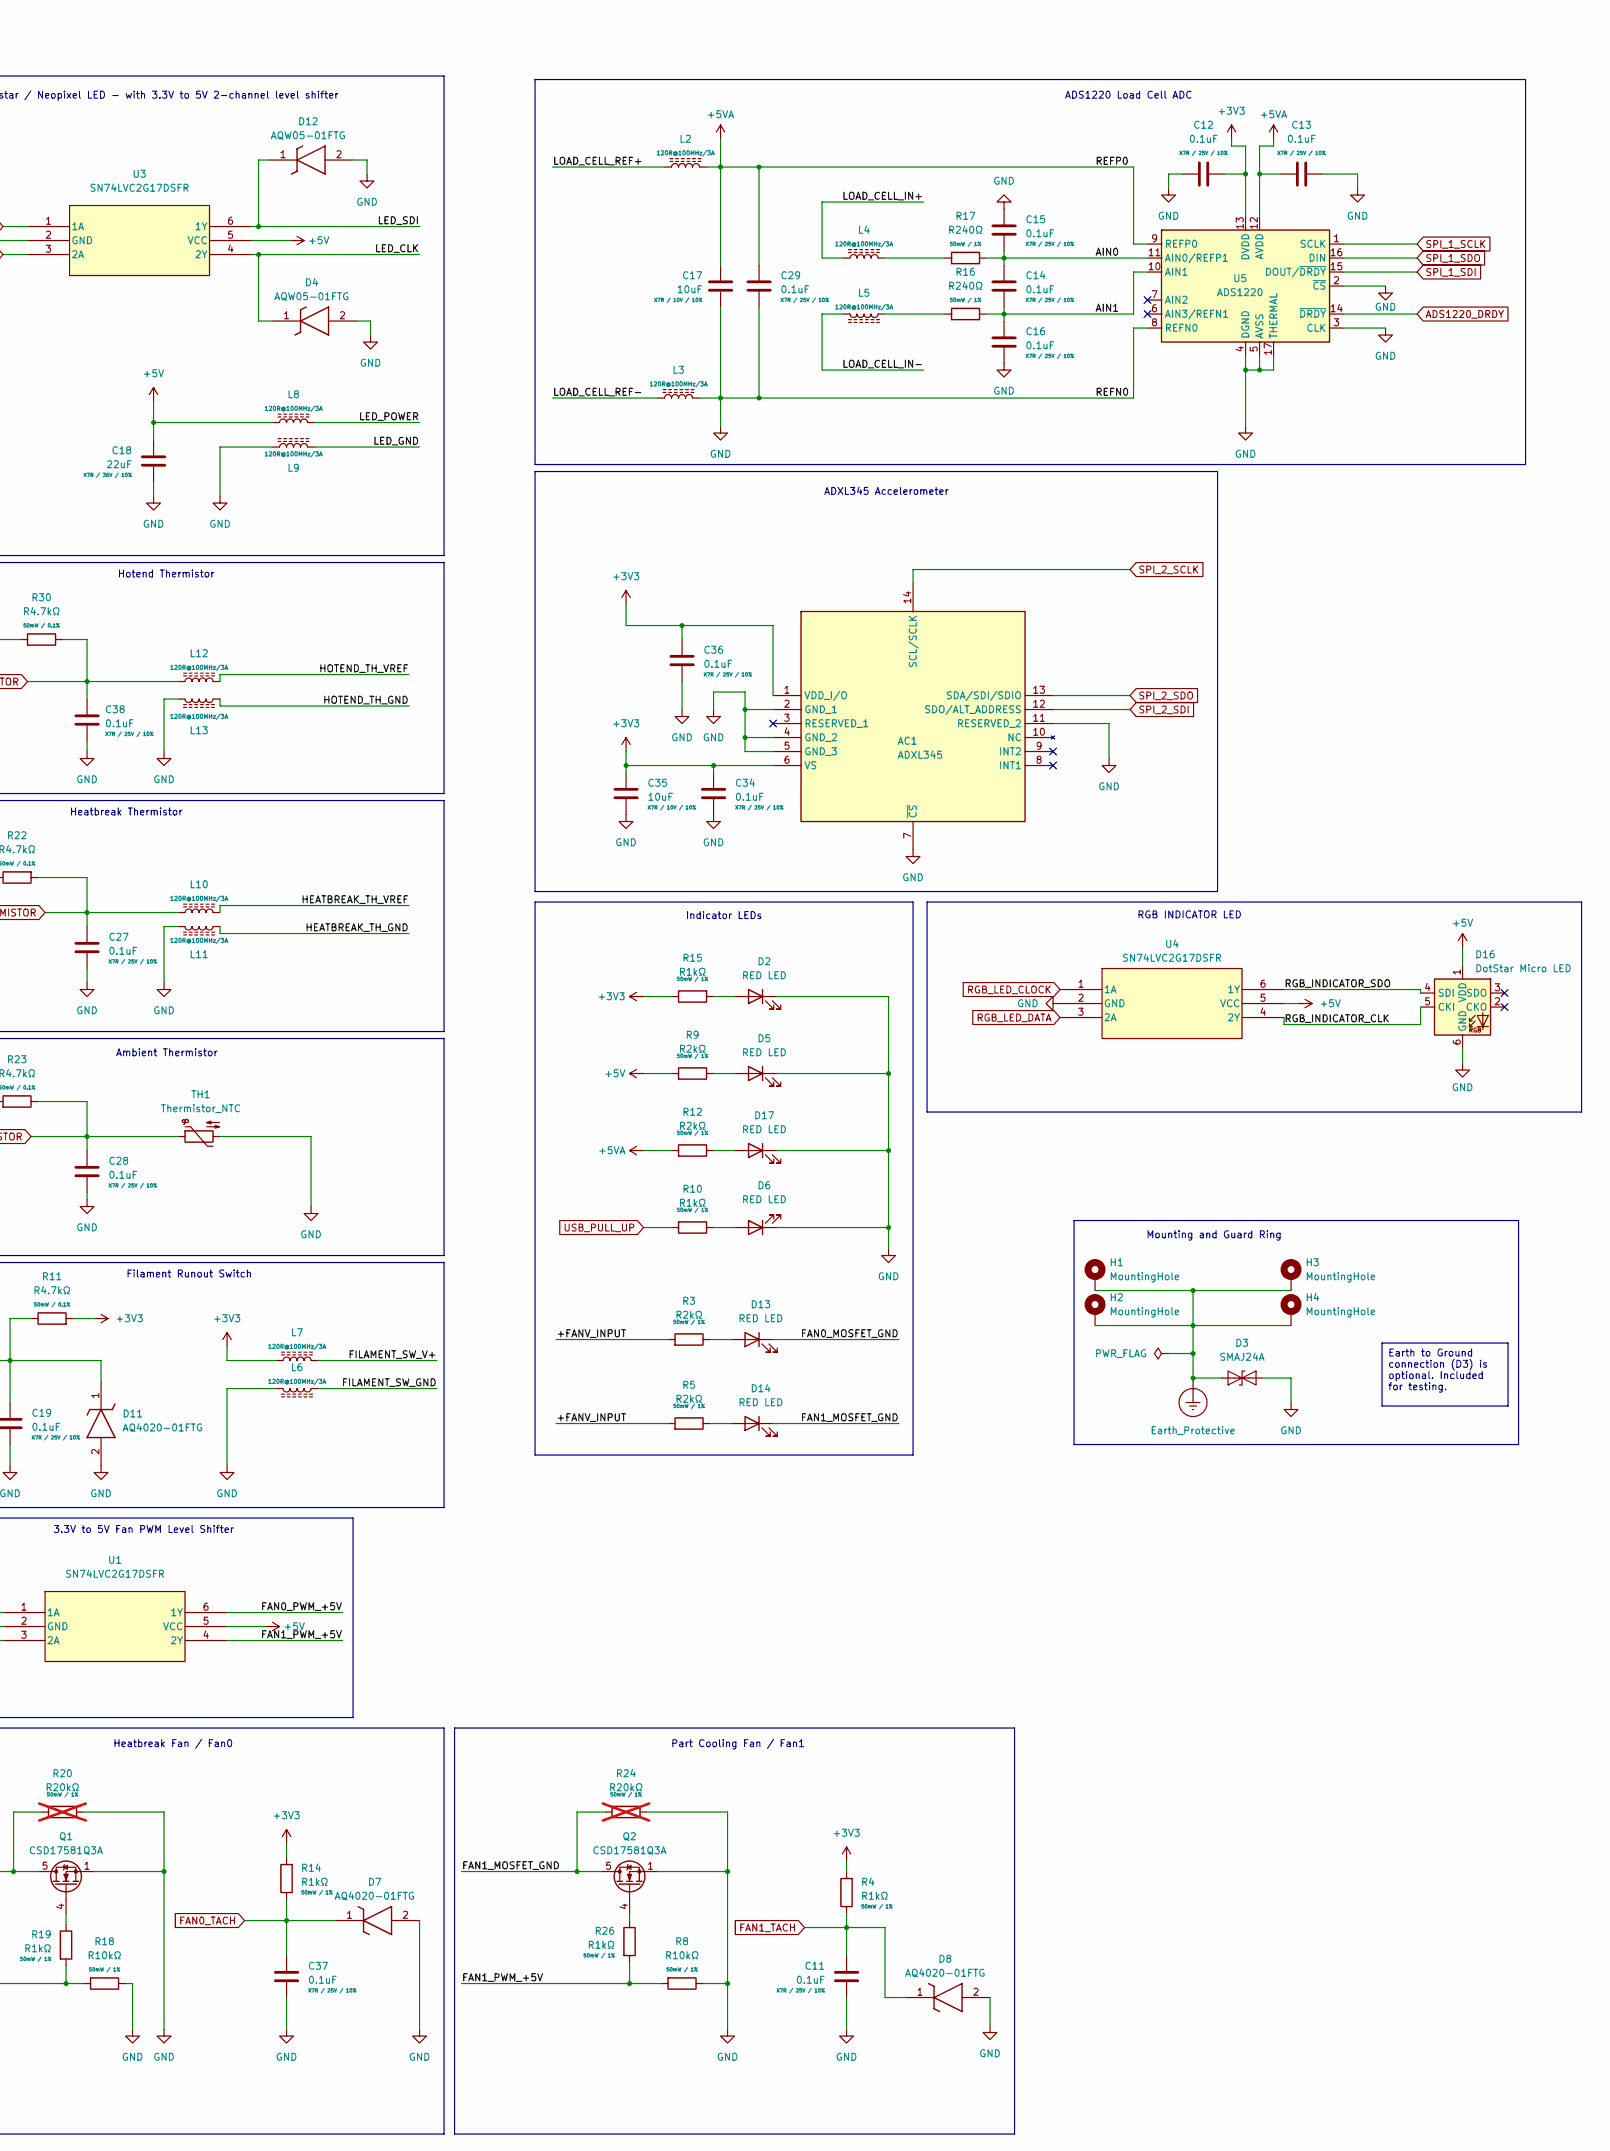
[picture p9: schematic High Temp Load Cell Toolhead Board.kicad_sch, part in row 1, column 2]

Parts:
AC1: ADXL345; Mouser Part Number N/A
C1, C7, C8, C18: 22uF; C_1206_3216Metric
C2: 1uF; C_0805_2012Metric
C3, C4, C5, C6, C9, C10, C17, C24, C35: 10uF; C_1206_3216Metric
C11, C12, C13, C14, C15, C16, C19, C20, C21, C22, C23, C25, C26, C27, C28, C29, C31, C32, C34, C36, C37, C38: 0.1uF; C_0603_1608Metric
C30, C33: 25pF; C_0603_1608Metric
D1, D3: SMAJ24A; D_SMA; Manufacturer_Part_Number SMAJ6A
D2, D5, D13, D14, D17: RED LED; LED_0603_1608Metric; Manufacturer_Part_Number LTST-C193KRKT-5A
D4, D12: AQW05-01FTG; SOD2613X114N; Manufacturer_Part_Number AQW05-01FTG
D6: RED LED; LED_0603_1608Metric; Part Number LTST-C193KRKT-5A
D7, D8, D11: AQ4020-01FTG; SOD2613X114N; Manufacturer_Part_Number AQ4020-01FTG; Mouser Part Number 576-AQ4020-01FTG
D9, D10: AQ4020-01FTG-C; SOD2613X114N; Manufacturer_Part_Number AQ4020-01FTG-C
D15: 40V, 1A, SMA; D_SMA; Manufacturer_Part_Number B140-13-F
D16: DotStar Micro LED; LED-APA102-2020; Part Number APA102-2020
H1, H2, H3, H4: MountingHole; MountingHole_3.2mm_M3_Pad_Via
J1, J11, J12: Conn_01x03; Molex_CLIK-Mate_505405-0370_1x03-1MP_P1.50mm_Vertical; Manufacturer_Part_Number 2132250370
J2: Conn_02x08; Molex_CLIK-Mate_213226-0610_1x06-1MP_P1.50mm_Horizontal; Manufacturer_Part_Number 2132271210
J6: Conn_01x04; Molex_CLIK-Mate_505405-0470_1x04-1MP_P1.50mm_Vertical; Manufacturer_Part_Number 2132250470
J7, J9: Conn_01x02; Molex_CLIK-Mate_505405-0270_1x02-1MP_P1.50mm_Vertical; Manufacturer_Part_Number 2132250230
J8: Conn_01x04; Molex_CLIK-Mate_505405-0470_1x04-1MP_P1.50mm_Vertical; Manufacturer_Part_Number 2132250370
J13: PinHeader_2x4_P2.54mm; PinHeader_2x03_P2.54mm_Vertical
L1, L2, L3, L4, L5, L6, L7, L8, L9, L10, L11, L12, L13: 120R@100MHz/3A; L_0805_2012Metric
LDO1, LDO3: TPS7A21-Q1 5V @ 500mA; VSON-8-1EP_3x3mm_P0.65mm_EP1.65x2.4mm_ThermalVias; Manufacturer_Part_Number TPS7A2150PQWDRBRQ1
LDO2: TPS7A21-Q1 3.3V @ 500mA; VSON-8-1EP_3x3mm_P0.65mm_EP1.65x2.4mm_ThermalVias; Manufacturer_Part_Number TPS7A2133PQWDRBRQ1
P1: USB_C_Plug_USB2.0; USB4145030170C; Manufacturer_Part_Number USB4145-03-0170-C
Q1, Q2: CSD17581Q3A; VSON-8_3.3x3.3mm_P0.65mm_NexFET; Manufacturer_Part_Number CSD17581Q3A
R1: R45.3kΩ; R_0603_1608Metric
R2, R8, R18, R27: R10kΩ; R_0603_1608Metric
R3, R5, R9, R12: R2kΩ; R_0603_1608Metric
R4, R10, R14, R15, R19, R26: R1kΩ; R_0603_1608Metric
R6, R7: R5.1kΩ; R_0603_1608Metric
R11, R22, R23, R30: R4.7kΩ; R_0603_1608Metric
R13, R33: R47Ω; R_0603_1608Metric
R16, R17: R240Ω; R_0603_1608Metric
R20, R24: R20kΩ; R_0603_1608Metric; not fitted
R21: R1.5kΩ; R_0603_1608Metric
SW1: SW_SPST; SW_SPST_PTS810; Manufacturer_Part_Number PTS810SJS250SMTR LFS
TH1: Thermistor_NTC; R_0603_1608Metric; Manufacturer_Part_Number SDNT1608X104F3950FTF
U1, U3, U4: SN74LVC2G17DSFR; SOT-363_SC-70-6; Mouser Part Number 771-LVC1G17GV125; LCSC C6076
U2: STM32F103CBU6TR; QFN-48-1EP_7x7mm_P0.5mm_EP5.6x5.6mm; Manufacturer_Part_Number STM32F103CBU6TR
U5: ADS1220; Texas_RSA_VQFN-16-1EP_4x4mm_P0.65mm_EP2.7x2.7mm; Manufacturer_Part_Number ADS1220IRVAR
VR1: TLVM23615RDNR; CONV_TLVM23615RDNR; Manufacturer_Part_Number TPSM861252RDXR
Y1: Crystal; XTAL_ECS-.327-6-34QCS-TR; Manufacturer_Part_Number ECS-.327-6-34QCS-TR

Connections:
+3V3: AC1.1 (VDD_I/O), AC1.6 (VS), C3.1, C12.2, C20.2, C21.2, C22.2, C23.2, C24.2, C25.2, C26.2, C31.1, C34.1, C35.1, C36.1, J13.2, J13.4, L7.1, LDO2.1 (VOUT), R4.2, R11.2, R14.2, R15.1, R22.1, R23.2, R30.2, U2.1 (VBAT), U2.9 (VDDA), U2.24 (VDD), U2.36 (VDD), U2.48 (VDD), U5.13 (DVDD)
+5V: C6.1, C18.1, D16.1 (VDD), L8.1, LDO1.1 (VOUT), R9.2, U1.5 (VCC), U3.5 (VCC), U4.5 (VCC)
+5V5: C4.1, C5.1, C7.1, C8.1, C9.1, LDO1.5 (EN), LDO1.8 (VIN), LDO2.5 (EN), LDO2.8 (VIN), LDO3.5 (EN), LDO3.8 (VIN), R1.1, VR1.4 (VOUT)
+5VA: C10.1, C13.2, C17.1, C29.1, L2.2, LDO3.1 (VOUT), R12.2, U5.9 (REFP0), U5.12 (AVDD)
+24V: C1.1, D15.1 (K), L1.2, VR1.2 (EN), VR1.3 (VIN)
/+5V_USB: D15.2 (A), P1.A4 (VBUS), P1.A9 (VBUS), P1.B4 (VBUS), P1.B9 (VBUS)
/+24V_INPUT: D1.1 (A1), J2.6, L1.1
/+FANV_INPUT: J1.3, J2.3, J11.3, R3.2, R5.2
/AIN0: C14.1, C15.2, R17.1, U5.11 (AIN0/REFP1)
/AIN1: C14.2, C16.1, R16.1, U5.10 (AIN1)
/FAN0_MOSFET_GND: D13.1 (K), J1.1, Q1.5 (D), R20.2
/FAN0_PWM_+5V: R18.2, R19.2, U1.6 (1Y)
/FAN1_MOSFET_GND: D14.1 (K), J11.1, Q2.5 (D), R24.2
/FAN1_PWM_+5V: R8.2, R26.2, U1.4 (2Y)
/FILAMENT_SW_GND: J12.3, L6.1
/FILAMENT_SW_V+: J12.1, L7.2
/HEATBREAK_TH_GND: J9.2, L11.1
/HEATBREAK_TH_VREF: J9.1, L10.1
/HOTEND_TH_GND: J7.2, L13.1
/HOTEND_TH_VREF: J7.1, L12.2
/LED_CLK: D4.1 (K), J8.3, U3.4 (2Y)
/LED_GND: J8.1, L9.1
/LED_POWER: J8.4, L8.2
/LED_SDI: D12.1 (K), J8.2, U3.6 (1Y)
/LOAD_CELL_IN+: J6.2, L4.1
/LOAD_CELL_IN-: J6.3, L5.2
/LOAD_CELL_REF+: J6.1, L2.1
/LOAD_CELL_REF-: J6.4, L3.1
/OSC_IN: C30.2, U2.5 (PD0), Y1.2
/OSC_OUT: C33.2, U2.6 (PD1), Y1.1
/RGB_INDICATOR_CLK: D16.5 (CKI), U4.4 (2Y)
/RGB_INDICATOR_SDO: D16.4 (SDI), U4.6 (1Y)
/SW_HEATSINK: VR1.5 (SW)
ADS1220_DRDY: U2.45 (PB8), U5.14 (~DRDY)
AMBIENT_THERMISTOR: C28.1, R23.1, TH1.1, U2.19 (PB1)
BOOT0: J13.1, R27.1, U2.44 (BOOT0)
DOTSTAR_LED_CLOCK: U2.43 (PB7), U3.3 (2A)
DOTSTAR_LED_DATA: U2.42 (PB6), U3.1 (1A)
Earth_Protective: D3.1 (A1), H1.1, H2.1, H3.1, H4.1, J1.MP (MountPin), J2.MP (MountPin), J6.MP (MountPin), J7.MP (MountPin), J8.MP (MountPin), J9.MP (MountPin), J11.MP (MountPin), J12.MP (MountPin)
FAN0_PWM: U1.1 (1A), U2.18 (PB0)
FAN0_TACH: C37.1, D7.1 (K), J1.2, R14.1, U2.14 (PA4)
FAN1_PWM: U1.3 (2A), U2.15 (PA5)
FAN1_TACH: C11.1, D8.1 (K), J11.2, R4.1, U2.13 (PA3)
FILAMENT_SW: C19.1, D11.1 (K), J12.2, R11.1, U2.17 (PA7)
GND: AC1.2 (GND_1), AC1.4 (GND_2), AC1.5 (GND_3), AC1.7 (~CS), AC1.11 (RESERVED_2), C1.2, C2.2, C3.2, C4.2, C5.2, C6.2, C7.2, C8.2, C9.2, C10.2, C11.2, C12.1, C13.1, C15.1, C16.2, C17.2, C18.2, C19.2, C20.1, C21.1, C22.1, C23.1, C24.1, C25.1, C26.1, C27.2, C28.2, C29.2, C30.1, C31.2, C32.2, C33.1, C34.2, C35.2, C36.2, C37.2, C38.2, D1.2 (A2), D2.1 (K), D3.2 (A2), D4.2 (A), D5.1 (K), D6.1 (K), D7.2 (A), D8.2 (A), D9.2 (A), D10.2 (A), D11.2 (A), D12.2 (A), D16.6 (GND), D17.1 (K), J2.4, J2.5, J13.6, L3.2, L6.2, L9.2, L11.2, L13.2, LDO1.2 (GND), LDO1.3 (GND), LDO1.4 (GND), LDO1.6 (GND), LDO1.7 (GND), LDO1.9 (GND), LDO2.2 (GND), LDO2.3 (GND), LDO2.4 (GND), LDO2.6 (GND), LDO2.7 (GND), LDO2.9 (GND), LDO3.2 (GND), LDO3.3 (GND), LDO3.4 (GND), LDO3.6 (GND), LDO3.7 (GND), LDO3.9 (GND), P1.A1 (GND), P1.A12 (GND), P1.B1 (GND), P1.B12 (GND), Q1.1 (S), Q1.2 (S), Q1.3 (S), Q2.1 (S), Q2.2 (S), Q2.3 (S), R2.2, R6.2, R7.2, R8.1, R18.1, R20.1, R24.1, R27.2, SW1.2 (B), TH1.2, U1.2 (GND), U2.8 (VSSA), U2.23 (VSS), U2.35 (VSS), U2.47 (VSS), U2.49 (VSS), U3.2 (GND), U4.2 (GND), U5.2 (~CS), U5.3 (CLK), U5.4 (DGND), U5.5 (AVSS), U5.8 (REFN0), U5.17 (THERMAL), VR1.1 (PGOOD), VR1.10 (GND), VR1.11 (RT)
HEATBREAK_THERMISTOR: C27.1, L10.2, R22.2, U2.16 (PA6)
HOTEND_THERMISTOR: C38.1, L12.1, R30.1, U2.12 (PA2)
NRST: C32.1, SW1.1 (A), U2.7 (NRST)
unnamed: D2.2 (A), R15.2
unnamed: D5.2 (A), R9.1
unnamed: D6.2 (A), R10.1
unnamed: D13.2 (A), R3.1
unnamed: D14.2 (A), R5.1
unnamed: D17.2 (A), R12.1
unnamed: L4.2, R17.2
unnamed: L5.1, R16.2
unnamed: P1.A5 (CC1), R6.1
unnamed: P1.B5 (CC2), R7.1
unnamed: Q1.4 (G), R19.1
unnamed: Q2.4 (G), R26.1
unnamed: R13.1, U2.39 (PB3)
unnamed: R33.1, U2.26 (PB13)
unnamed: R1.2, R2.1, VR1.9 (FB)
unnamed: C2.1, VR1.8 (VCC)
RGB_LED_CLOCK: U2.29 (PA8), U4.1 (1A)
RGB_LED_DATA: U2.30 (PA9), U4.3 (2A)
SPI_1_SCLK: R13.2, U5.1 (SCLK)
SPI_1_SDI: U2.40 (PB4), U5.15 (DOUT/~DRDY)
SPI_1_SDO: U2.41 (PB5), U5.16 (DIN)
SPI_2_SCLK: AC1.14 (SCL/SCLK), R33.2
SPI_2_SDI: AC1.12 (SDO/ALT_ADDRESS), U2.27 (PB14)
SPI_2_SDO: AC1.13 (SDA/SDI/SDIO), U2.28 (PB15)
SWD_IO: J13.5, U2.34 (PA13)
SW_CLK: J13.3, U2.37 (PA14)
USB_D+: D9.1 (K), J2.1, P1.A6 (D+), P1.B6 (D+), R21.2, U2.32 (PA11)
USB_D-: D10.1 (K), J2.2, P1.A7 (D-), P1.B7 (D-), U2.33 (PA12)
USB_PULL_UP: R10.2, R21.1, U2.31 (PA10)

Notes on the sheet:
Earth to Ground connection (D3) is optional. Included for testing.
5.5V to 5V LED Power LDO
3.3V to 5V Fan PWM Level Shifter
MCU
Heatbreak Thermistor
USB Data Line ESD and Full Speed Pull-Up
Indicator LEDs
ADS1220 Load Cell ADC
5.5V to 3.3V LDO
Hotend Thermistor
Dotstar / Neopixel LED - with 3.3V to 5V 2-channel level shifter
Filament Runout Switch
Heatbreak Fan / Fan0
Ambient Thermistor
12V Power Input ESD and Conditioning
RGB INDICATOR LED
5.5V to 5V Load Cell Power LDO
USBC Connector (Optional)
12V to 5.5V Switching Buck Converter Module
Part Cooling Fan / Fan1
Connectors
Mounting and Guard Ring
Single Wire (SW) Debug Port
ADXL345 Accelerometer
Reset Switch

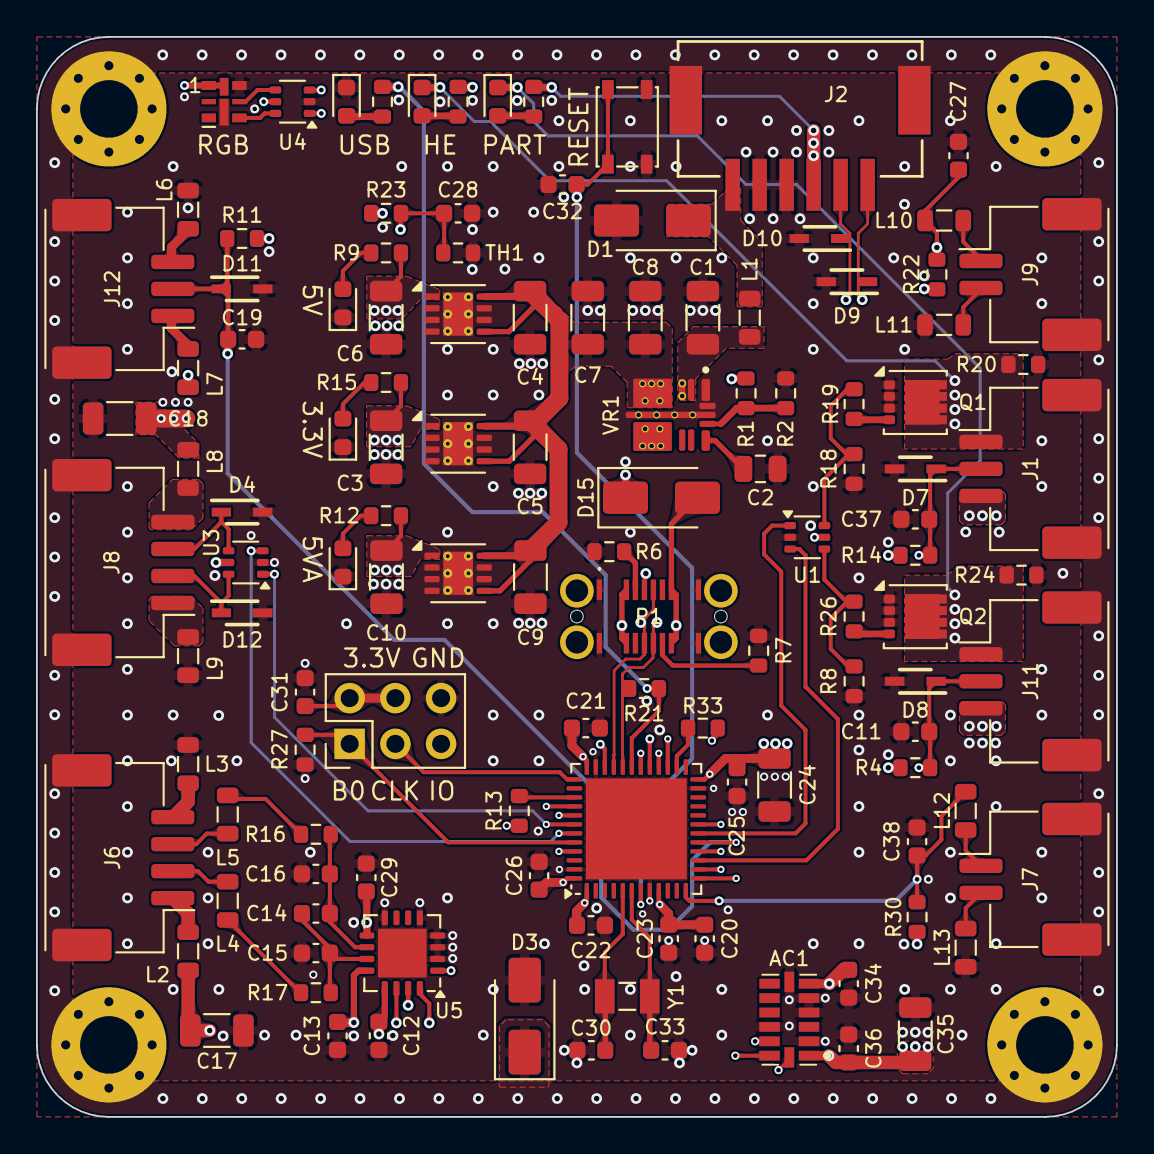
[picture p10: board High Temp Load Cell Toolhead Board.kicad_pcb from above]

Board: 6 copper layers, 60.0 x 60.0 mm, 125 parts (0 on the bottom side), 76 nets.

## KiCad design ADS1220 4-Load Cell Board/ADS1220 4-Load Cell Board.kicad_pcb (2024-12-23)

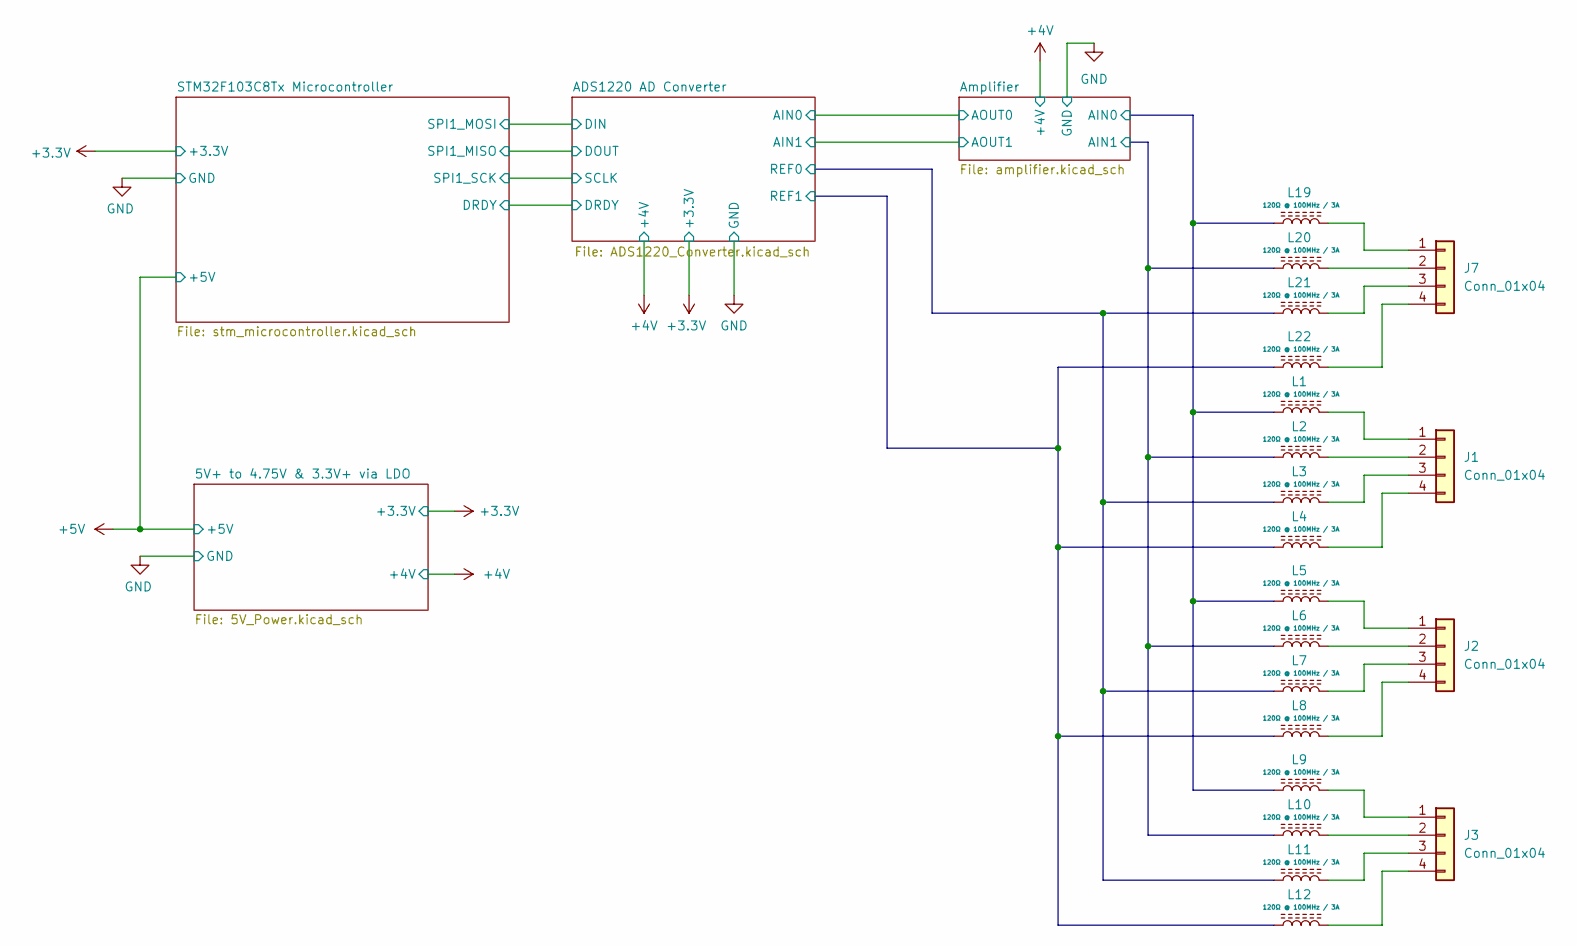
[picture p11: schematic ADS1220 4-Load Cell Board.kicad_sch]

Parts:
J1, J2, J3, J7: Conn_01x04; JST_XH_B4B-XH-A_1x04_P2.50mm_Vertical
L1, L2, L3, L4, L5, L6, L7, L8, L9, L10, L11, L12, L19, L20, L21, L22: 120Ω @ 100MHz / 3A; L_0805_2012Metric_Pad1.05x1.20mm_HandSolder

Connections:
+4V: L3.1, L7.1, L11.1, L21.1; also elsewhere on the board
/Amplifier/AIN0: L1.1, L5.1, L9.1, L19.1; also elsewhere on the board
/Amplifier/AIN1: L2.1, L6.1, L10.1, L20.1; also elsewhere on the board
GND: L4.1, L8.1, L12.1, L22.1; also elsewhere on the board
unnamed: J1.1, L1.2
unnamed: J1.2, L2.2
unnamed: J1.3, L3.2
unnamed: J1.4, L4.2
unnamed: J2.1, L5.2
unnamed: J2.2, L6.2
unnamed: J2.3, L7.2
unnamed: J2.4, L8.2
unnamed: J3.1, L9.2
unnamed: J3.2, L10.2
unnamed: J3.3, L11.2
unnamed: J3.4, L12.2
unnamed: J7.1, L19.2
unnamed: J7.2, L20.2
unnamed: J7.3, L21.2
unnamed: J7.4, L22.2

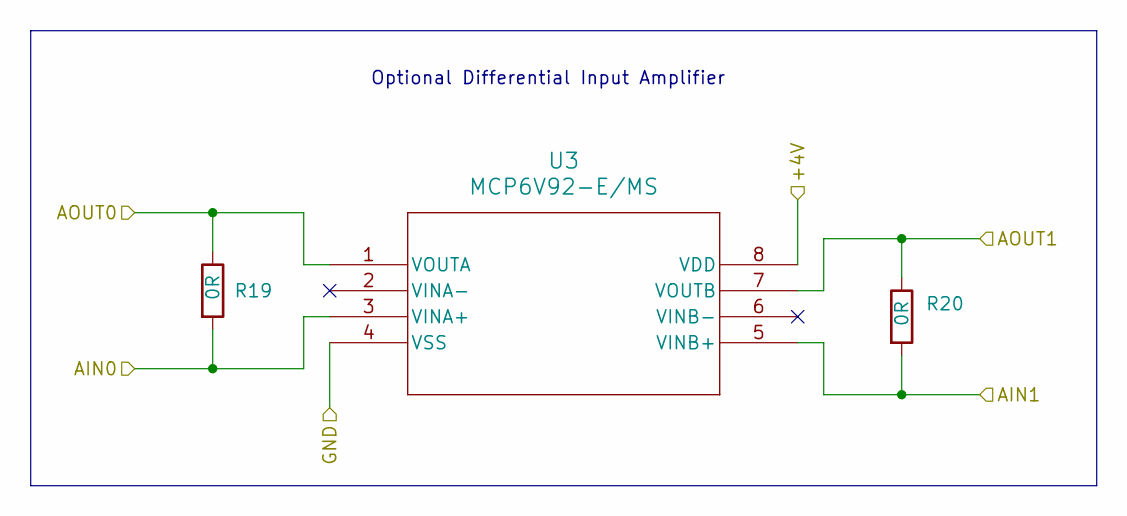
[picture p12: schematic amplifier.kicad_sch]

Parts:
R19, R20: 0R; R_0805_2012Metric_Pad1.20x1.40mm_HandSolder
U3: MCP6V92-E/MS; MSOP8_MS_MCH

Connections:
+4V: U3.8 (VDD); also elsewhere on the board
/ADS1220 AD Converter/AIN0: R19.1, U3.1 (VOUTA); also elsewhere on the board
/ADS1220 AD Converter/AIN1: R20.1, U3.7 (VOUTB); also elsewhere on the board
/Amplifier/AIN0: R19.2, U3.3 (VINA+); also elsewhere on the board
/Amplifier/AIN1: R20.2, U3.5 (VINB+); also elsewhere on the board
GND: U3.4 (VSS); also elsewhere on the board

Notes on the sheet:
Optional Differential Input Amplifier

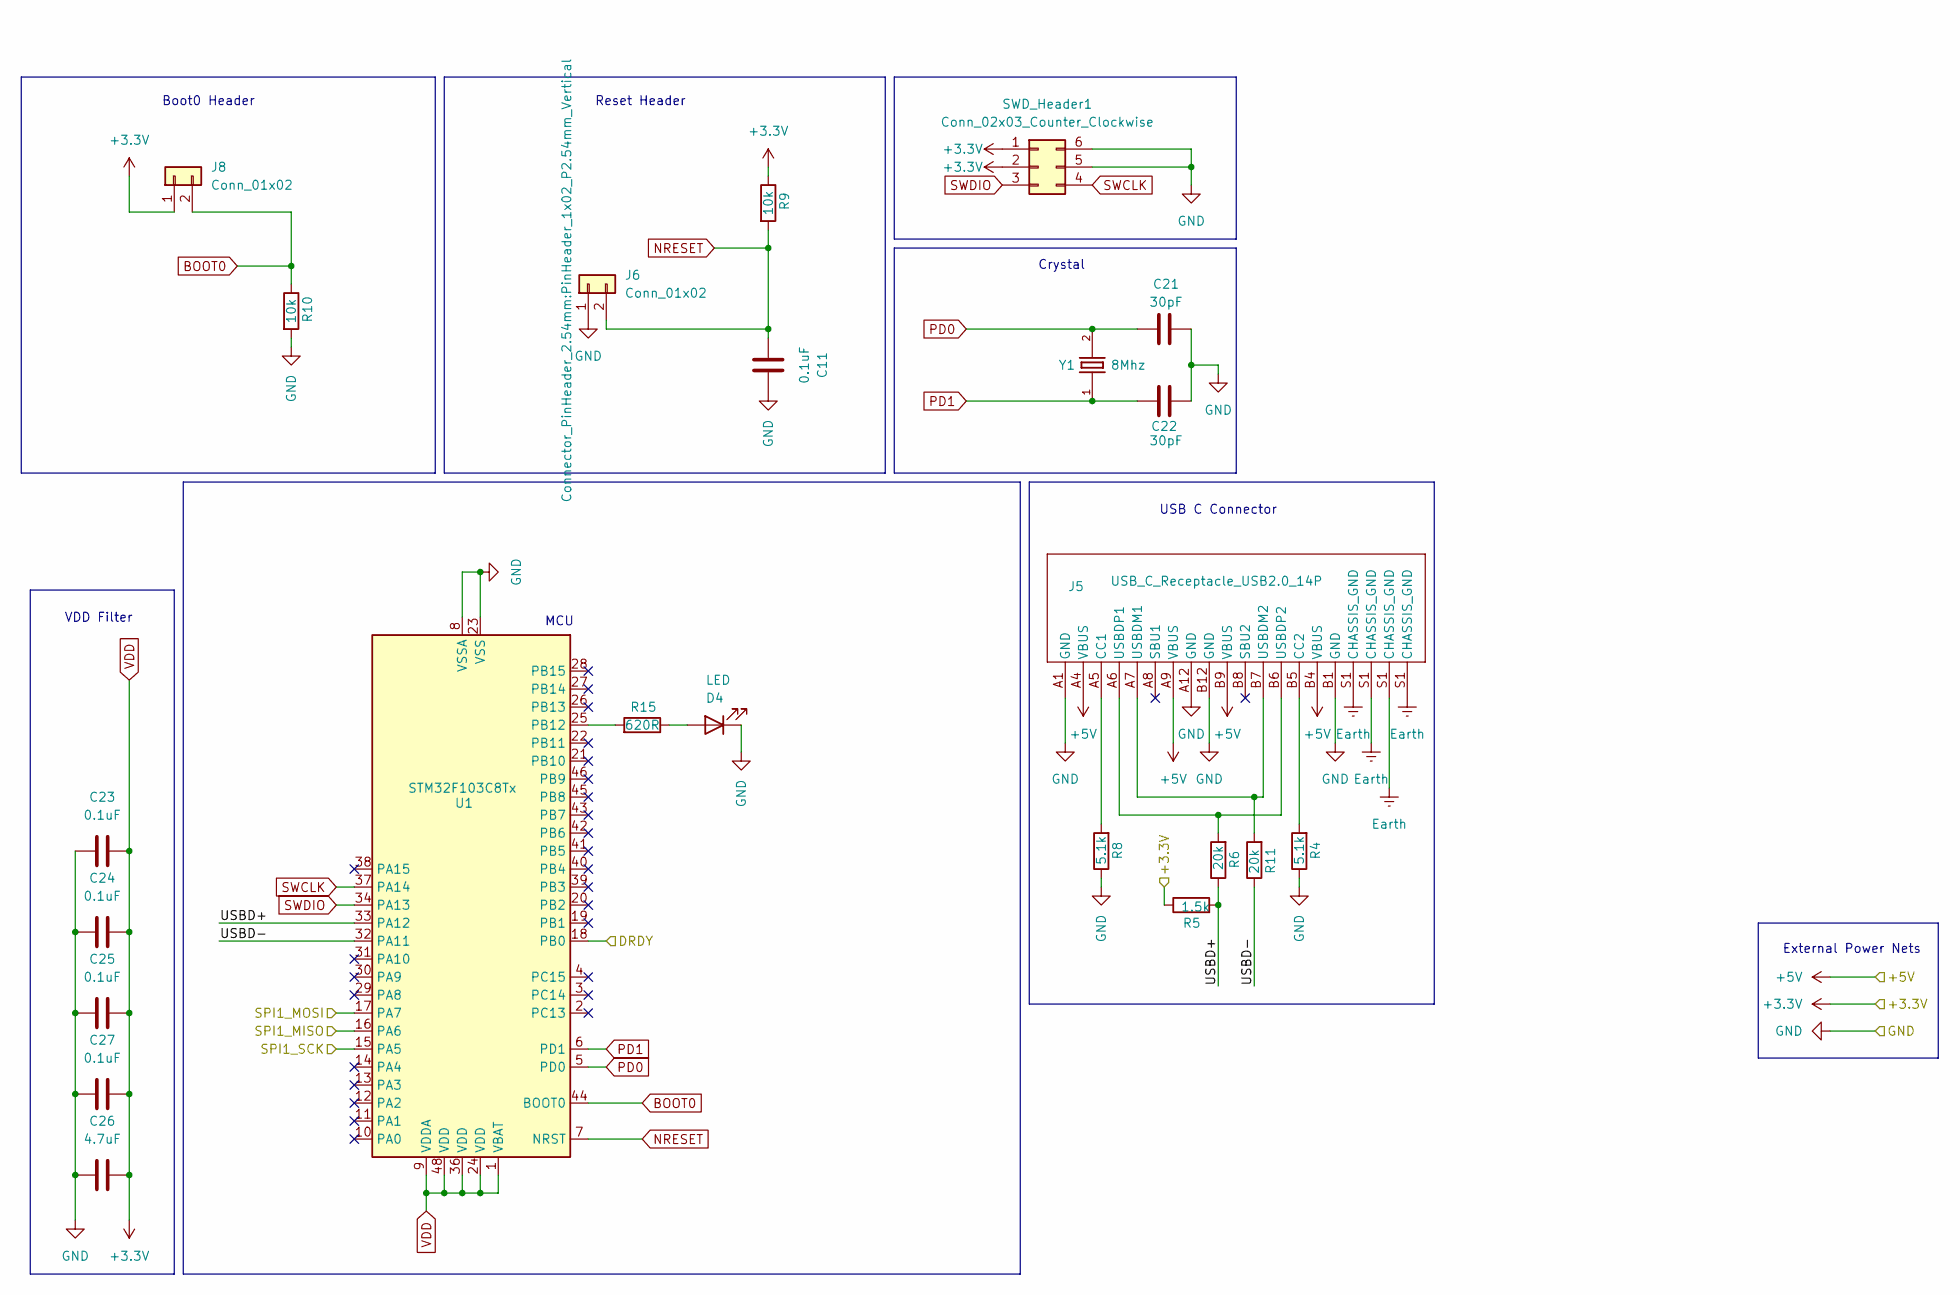
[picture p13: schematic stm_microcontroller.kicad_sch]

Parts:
C11, C23, C24, C25, C27: 0.1uF; C_0805_2012Metric_Pad1.18x1.45mm_HandSolder
C21, C22: 30pF; C_0805_2012Metric_Pad1.18x1.45mm_HandSolder
C26: 4.7uF; C_0805_2012Metric_Pad1.18x1.45mm_HandSolder
D4: LED; LED_1206_3216Metric_Pad1.42x1.75mm_HandSolder
J5: USB_C_Receptacle_USB2.0_14P; USB_C_Receptacle_GCT_USB4085
J6, J8: Conn_01x02; PinHeader_1x02_P2.54mm_Vertical
R4, R8: 5.1k; R_0805_2012Metric_Pad1.20x1.40mm_HandSolder
R5: 1.5k; R_0805_2012Metric_Pad1.20x1.40mm_HandSolder
R6, R11: 20k; R_0805_2012Metric_Pad1.20x1.40mm_HandSolder
R9, R10: 10k; R_0805_2012Metric_Pad1.20x1.40mm_HandSolder
R15: 620R; R_0805_2012Metric_Pad1.20x1.40mm_HandSolder
SWD_Header1: Conn_02x03_Counter_Clockwise; PinHeader_2x03_P2.54mm_Vertical
U1: STM32F103C8Tx; LQFP48_STM
Y1: 8Mhz; XTAL_ECS-80-18-30-JGN-TR; PARTREV 2017

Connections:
+3.3V: C23.2, C24.2, C25.2, C26.2, C27.2, J8.1, R5.1, R9.1, SWD_Header1.1, SWD_Header1.2, U1.1 (VBAT), U1.9 (VDDA), U1.24 (VDD), U1.36 (VDD), U1.48 (VDD); also elsewhere on the board
+5V: J5.A4 (VBUS), J5.A9 (VBUS), J5.B4 (VBUS), J5.B9 (VBUS); also elsewhere on the board
/ADS1220 AD Converter/DIN: U1.17 (PA7); also elsewhere on the board
/ADS1220 AD Converter/DOUT: U1.16 (PA6); also elsewhere on the board
/ADS1220 AD Converter/DRDY: U1.18 (PB0); also elsewhere on the board
/ADS1220 AD Converter/SCLK: U1.15 (PA5); also elsewhere on the board
/STM32F103C8Tx Microcontroller/USBD+: R5.2, R6.1, U1.33 (PA12)
/STM32F103C8Tx Microcontroller/USBD-: R11.1, U1.32 (PA11)
BOOT0: J8.2, R10.1, U1.44 (BOOT0)
Earth: J5.S1 (CHASSIS_GND)
GND: C11.2, C21.2, C22.1, C23.1, C24.1, C25.1, C26.1, C27.1, D4.1 (K), J5.A1 (GND), J5.A12 (GND), J5.B1 (GND), J5.B12 (GND), J6.1, R4.1, R8.1, R10.2, SWD_Header1.5, SWD_Header1.6, U1.8 (VSSA), U1.23 (VSS), U1.35 (VSS), U1.47 (VSS); also elsewhere on the board
NRESET: C11.1, J6.2, R9.2, U1.7 (NRST)
unnamed: D4.2 (A), R15.1
unnamed: J5.A5 (CC1), R8.2
unnamed: J5.B5 (CC2), R4.2
unnamed: J5.A7 (USBDM1), J5.B7 (USBDM2), R11.2
unnamed: J5.A6 (USBDP1), J5.B6 (USBDP2), R6.2
unnamed: R15.2, U1.25 (PB12)
PD0: C21.1, U1.5 (PD0), Y1.2
PD1: C22.2, U1.6 (PD1), Y1.1
SWCLK: SWD_Header1.4, U1.37 (PA14)
SWDIO: SWD_Header1.3, U1.34 (PA13)

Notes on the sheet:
Reset Header
USB C Connector
Crystal
Boot0 Header
MCU
VDD Filter
External Power Nets

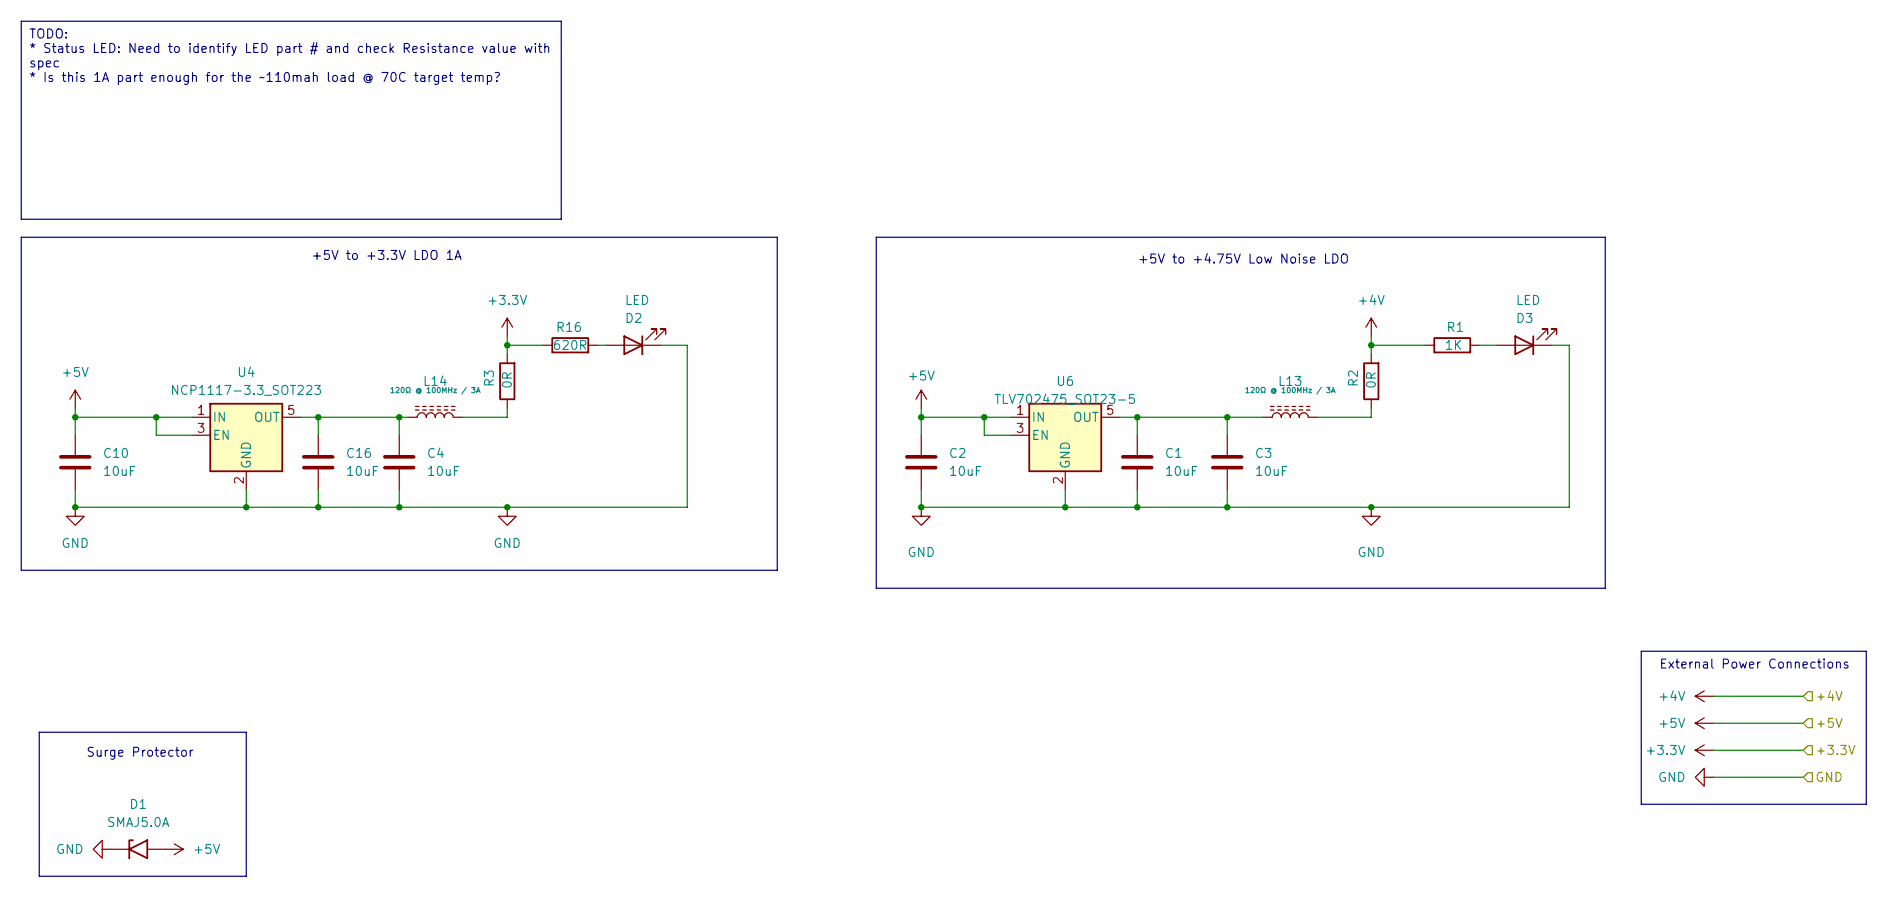
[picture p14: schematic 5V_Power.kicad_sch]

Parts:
C1, C2, C3, C4, C10, C16: 10uF; C_0805_2012Metric_Pad1.18x1.45mm_HandSolder
D1: SMAJ5.0A; D_SMA
D2, D3: LED; LED_1206_3216Metric_Pad1.42x1.75mm_HandSolder
L13, L14: 120Ω @ 100MHz / 3A; L_0805_2012Metric_Pad1.05x1.20mm_HandSolder
R1: 1K; R_0805_2012Metric_Pad1.20x1.40mm_HandSolder
R2, R3: 0R; R_0805_2012Metric_Pad1.20x1.40mm_HandSolder
R16: 620R; R_0805_2012Metric_Pad1.20x1.40mm_HandSolder
U4: NCP1117-3.3_SOT223; SOT-23-5
U6: TLV702475_SOT23-5; SOT-23-5_HandSoldering

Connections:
+3.3V: R3.2, R16.1; also elsewhere on the board
+4V: R1.1, R2.2; also elsewhere on the board
+5V: C2.1, C10.1, D1.2 (A2), U4.1 (IN), U4.3 (EN), U6.1 (IN), U6.3 (EN); also elsewhere on the board
GND: C1.2, C2.2, C3.2, C4.2, C10.2, C16.2, D1.1 (A1), D2.1 (K), D3.1 (K), U4.2 (GND), U6.2 (GND); also elsewhere on the board
unnamed: D2.2 (A), R16.2
unnamed: D3.2 (A), R1.2
unnamed: L13.2, R2.1
unnamed: L14.2, R3.1
unnamed: C4.1, C16.1, L14.1, U4.5 (OUT)
unnamed: C1.1, C3.1, L13.1, U6.5 (OUT)

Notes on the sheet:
TODO: * Status LED: Need to identify LED part # and check Resistance value with spec * Is this 1A part enough for the ~110mah load @ 70C target temp?
Surge Protector
External Power Connections
+5V to +3.3V LDO 1A
+5V to +4.75V Low Noise LDO

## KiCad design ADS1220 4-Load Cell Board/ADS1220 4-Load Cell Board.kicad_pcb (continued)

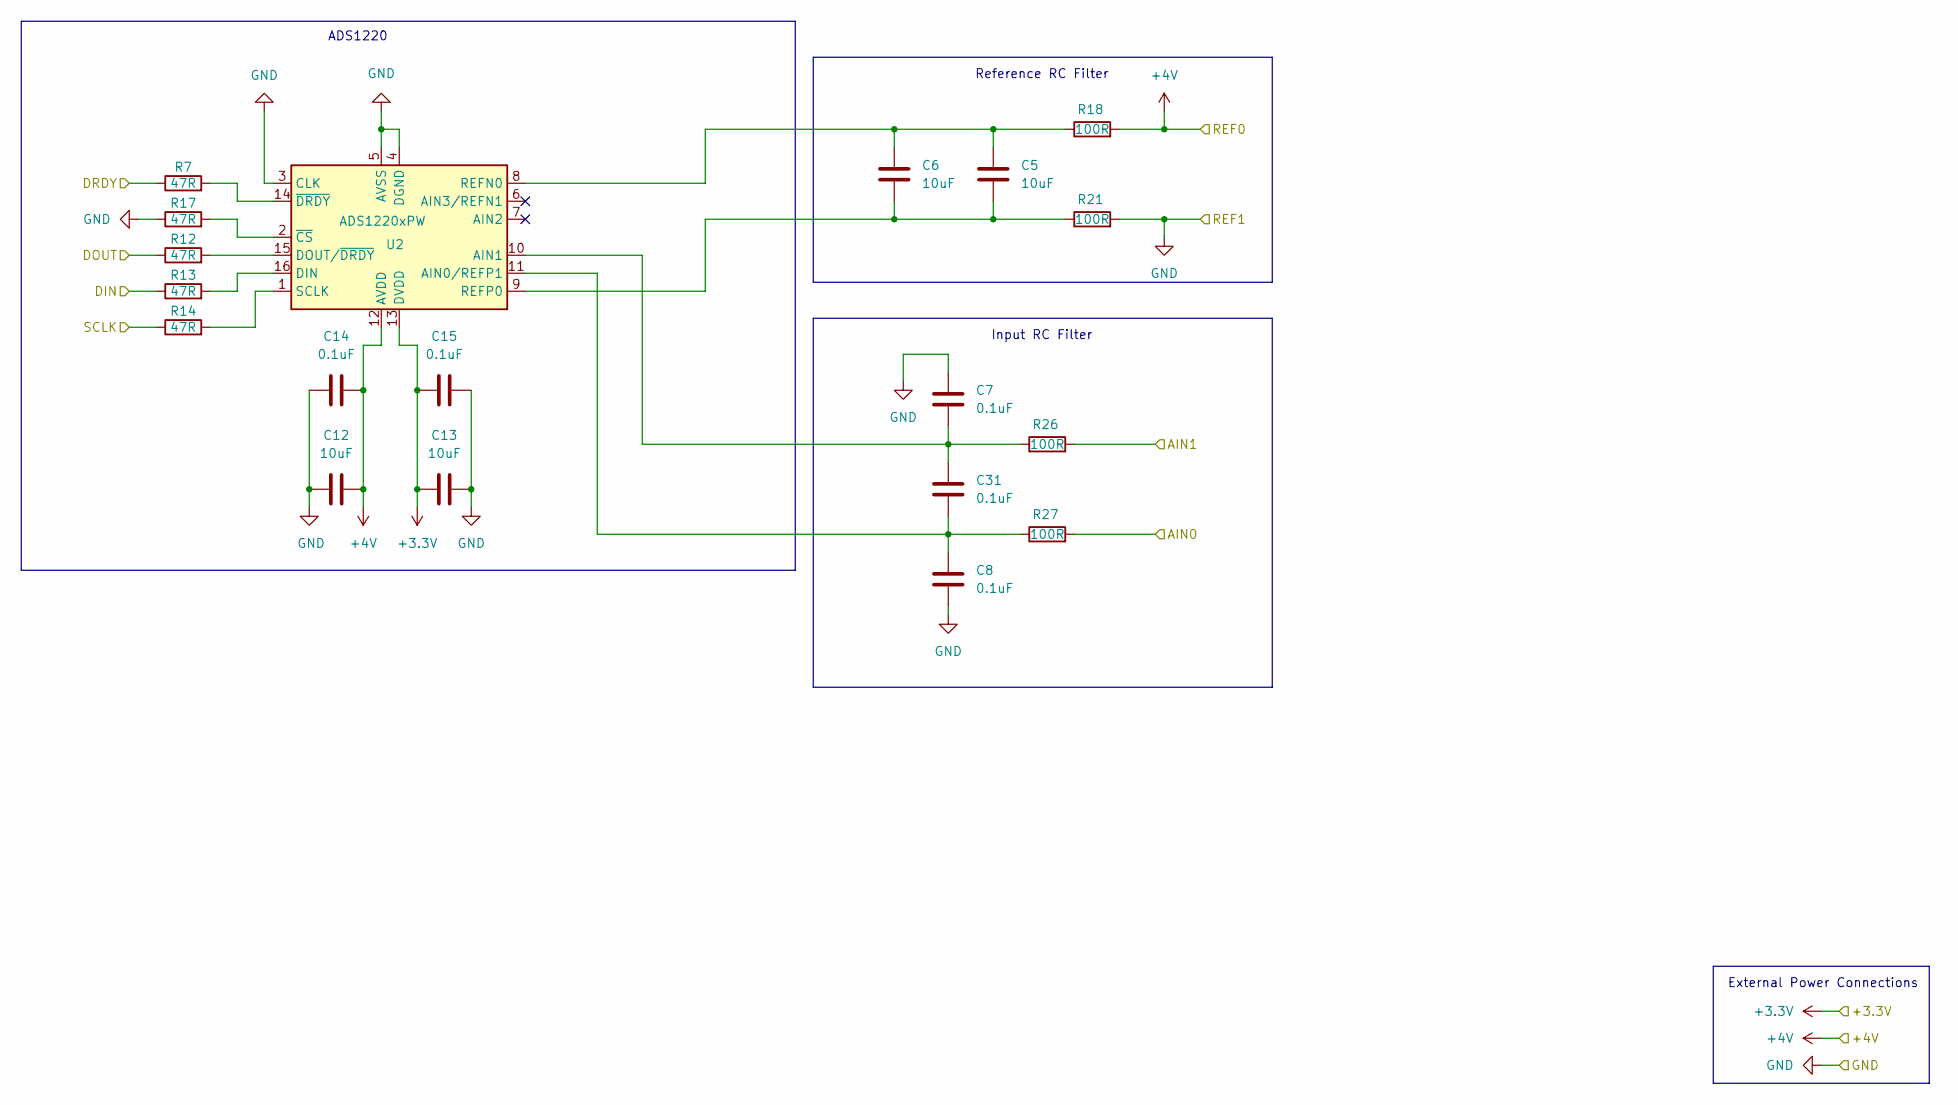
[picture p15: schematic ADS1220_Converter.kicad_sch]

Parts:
C5, C6, C12, C13: 10uF; C_0805_2012Metric_Pad1.18x1.45mm_HandSolder
C7, C8, C14, C15, C31: 0.1uF; C_0805_2012Metric_Pad1.18x1.45mm_HandSolder
R7, R12, R13, R14, R17: 47R; R_0805_2012Metric_Pad1.20x1.40mm_HandSolder
R18, R21, R26, R27: 100R; R_0805_2012Metric_Pad1.20x1.40mm_HandSolder
U2: ADS1220xPW; TSSOP-16_4.4x5mm_P0.65mm

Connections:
+3.3V: C13.1, C15.1, U2.13 (DVDD); also elsewhere on the board
+4V: C12.2, C14.2, R18.2, U2.12 (AVDD); also elsewhere on the board
/ADS1220 AD Converter/AIN0: R27.2; also elsewhere on the board
/ADS1220 AD Converter/AIN1: R26.2; also elsewhere on the board
/ADS1220 AD Converter/DIN: R13.1; also elsewhere on the board
/ADS1220 AD Converter/DOUT: R12.1; also elsewhere on the board
/ADS1220 AD Converter/DRDY: R7.1; also elsewhere on the board
/ADS1220 AD Converter/SCLK: R14.1; also elsewhere on the board
GND: C7.1, C8.2, C12.1, C13.2, C14.1, C15.2, R17.1, R21.2, U2.3 (CLK), U2.4 (DGND), U2.5 (AVSS); also elsewhere on the board
unnamed: C8.1, C31.2, R27.1, U2.11 (AIN0/REFP1)
unnamed: C7.2, C31.1, R26.1, U2.10 (AIN1)
unnamed: R13.2, U2.16 (DIN)
unnamed: R12.2, U2.15 (DOUT/~DRDY)
unnamed: C5.1, C6.1, R18.1, U2.8 (REFN0)
unnamed: C5.2, C6.2, R21.1, U2.9 (REFP0)
unnamed: R14.2, U2.1 (SCLK)
unnamed: R17.2, U2.2 (~CS)
unnamed: R7.2, U2.14 (~DRDY)

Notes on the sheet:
ADS1220
Reference RC Filter
Input RC Filter
External Power Connections

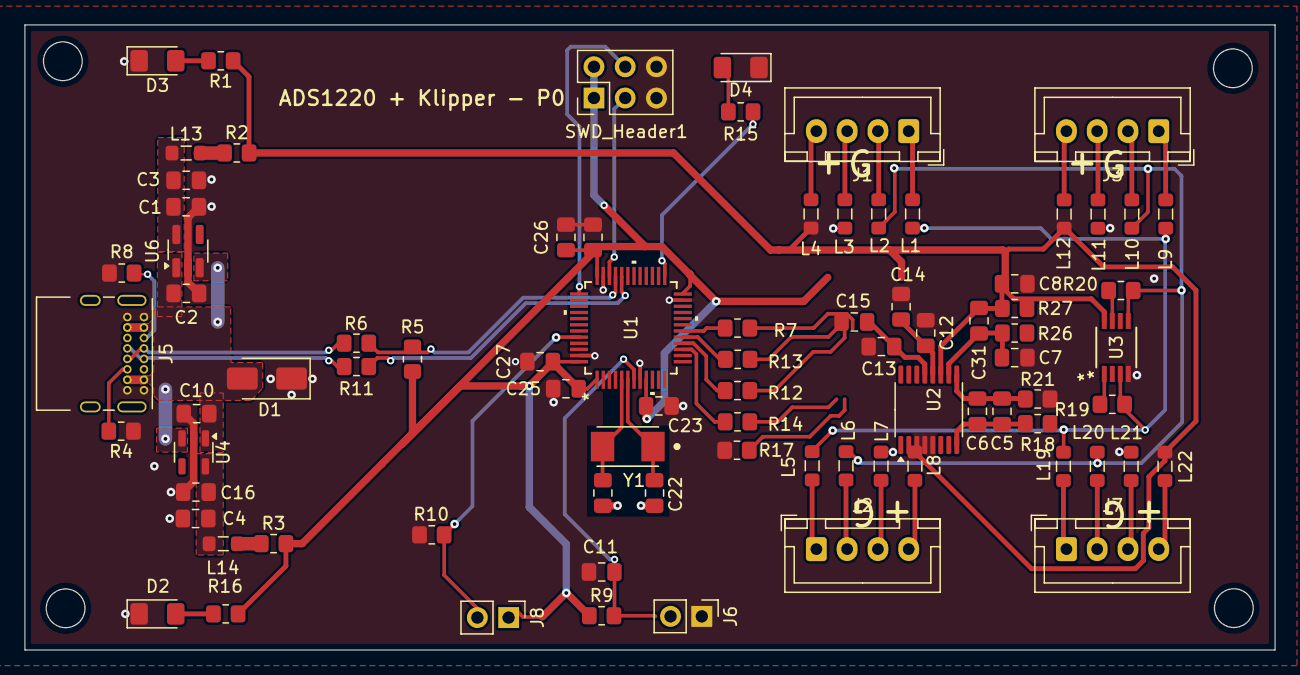
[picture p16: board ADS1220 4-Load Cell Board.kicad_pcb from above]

Board: 2 copper layers, 101.6 x 50.8 mm, 82 parts (0 on the bottom side), 57 nets.

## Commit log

2024-08-15 Add KiCad Project Files
    [3.3V_Power.kicad_sch, 5V_Power.kicad_sch, ADS1220 4-Load Cell Board.kicad_pcb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]
2024-08-15 Add MCP6V92 Amplifier
    Add amplifier part to amplifier block
    [ADS1220 4-Load Cell Board.kicad_sch, amplifier.kicad_sch]
2024-08-15 Add bypass resistors for Amplifier
    Add 0R resistor pads to allow the amplifier to be bypassed so we can test with/without it in the circuit.
    [ADS1220 4-Load Cell Board.kicad_sch, amplifier.kicad_sch]
2024-08-17 Use 12V Power
    * Use 12 V Power
    * Update to an F103 processor with better compatibility with Katapult
    [3.3V_Power.kicad_sch, 5V_Power.kicad_sch, ADS1220 4-Load Cell Board.kicad_sch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]
2024-08-18 Update 5V Power Stage
    * Update the 5V power stage based on the recommendations from TI.
    * Updated standard passive footprint to 0805 hand solder configuration
    [5V_Power.kicad_sch, ADS1220_Converter.kicad_sch, amplifier.kicad_sch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]
2024-08-19 Initial Routing
    Taking a first pass at layout of the PCB
    * load cell connectors were moved to the root schematic and placed on a bus to facilitate PCB routing
    * Nets for the filters were directly connected to remove the confusion about GND verses REFN
    [ADS1220 4-Load Cell Board.kicad_pcb, ADS1220 4-Load Cell Board.kicad_sch, ADS1220_Converter.kicad_sch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]
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2024-08-20 Fix amplifier footprint
    shrink pads to they can be produced on 0.2mm process
    [ADS1220 4-Load Cell Board.kicad_pcb]
2024-08-20 Update USB Connector
    Update USB connector and design rules so it passes inspection.
    [ADS1220 4-Load Cell Board.kicad_pcb]
2024-08-20 Update Switch Footprints
    Update switch schematic and footprint to match the actual part being used
    [ADS1220 4-Load Cell Board.kicad_pcb, stm_microcontroller.kicad_sch]
2024-08-20 Update Crystal
    Change crystal footprint to ABM3-8.000MHZ-B4Y-T
    [ADS1220 4-Load Cell Board.kicad_pcb]
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2024-08-21 Convert Power to LDOs
    Convert power section to use only LDOs. This means we will only get 4.75V or 4.5V on the analog line but this comes with greatly increased simplicity of layout.
    [5V_Power.kicad_sch, ADS1220 4-Load Cell Board.kicad_pcb, ADS1220 4-Load Cell Board.kicad_sch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]
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2024-08-22 Add Single Wire Debug
    * Add Single Wire Debug (SWD) Tag Connect Connector
    * Re-layout of 5V power so the 5V pins connect to a pad directly behind the USB connector
    * Add 0R resistors to air gap the 3.3V and 5V power rails for incremental board bringup
    * Rotate ADS1220 for cleaner layout
    * Remove connections to reference voltage pins, since AVDD/AVSS is a valid reference
    fixup
    fixup
    fixup
    [5V_Power.kicad_sch, ADS1220 4-Load Cell Board.kicad_pcb, ADS1220 4-Load Cell Board.kicad_sch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]
2024-08-23 USB Improvements
    * Changed the USB connector symbol and rebuilt it to have pins that match the pads
    * Set up the USB lines as a differential pair
    * VIA Stitch the board
    * Increased minimum trace width to 0.3mm
    [ADS1220 4-Load Cell Board.kicad_pcb, ADS1220 4-Load Cell Board.kicad_sch, stm_microcontroller.kicad_sch]
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2024-08-24 Crystal Changes
    * Update crystal selection, schematic and footprint
    * Add resistor to limit drive current to crystal
    * Block ground plane fill under crystal circuit
    [ADS1220 4-Load Cell Board.kicad_pcb, ADS1220 4-Load Cell Board.kicad_sch, ADS1220_Converter.kicad_sch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]
2024-08-24 Update Rext value
    1.1k is an approximate value for the resistance required.
    [stm_microcontroller.kicad_sch]
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2024-12-23 High Temp Toolhead Board
    * Move different boards to directories
    * check in the High Temp Tool Board work
    delete autosaves
    [3.3V_Power.kicad_sch, 5V_Power.kicad_sch, ADS1220 4-Load Cell Board.kicad_pcb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]
2024-12-24 Fix Incorrect Power Connections to ADXL or Gate
    GND and VIN were reversed
    [High Temp Load Cell Toolhead Board.kicad_pcb, High Temp Load Cell Toolhead Board.kicad_sch]
2024-12-31 Re-work PCB for Grids
    * Lay out components consistently using a 0.2mm grid
    * Removes all grids that are not divisible by 0.1mm (gets rid of 'off by 0.05 errors')
    * Brought back some more dense layouts with rows of components
    * Reset all reference text positions so they align with components consistently
    * References don't intersect with vias
    * Improve how some traces enter/exit the chips using smaller vias and traces
    * Removed resistor on the LED clock line as its not needed (klipper doesn't use real SPI for Dotstar)
    [High Temp Load Cell Toolhead Board.kicad_pcb, High Temp Load Cell Toolhead Board.kicad_sch]
2024-12-31 Filet Edgecuts
    Makes corners of the board have a 4mm radius
    [High Temp Load Cell Toolhead Board.kicad_pcb]
2024-12-31 Cleanup Zone Fills
    * Cleaned up the zone fills and component positioning for the LDOs. Now they are on the grid and identical copies of each other
    * Added a pad on layers 2, 3 & 4 under the no-connect pad 5 on the switching regulator for better thermal transfer.
    * Cleaned up some ground pours around the MCU. Some traces caused islands or choking of the ground pins.
    * Tweaked some text placement to better avoid vias and be less ambiguous
    * Earth Protective zone now removes islands.
    * Eliminated a choked zone in the 3.3V power plane by routing ADS1220_DRDY on both layer 2 and 3. Since this isn't a high speed signal this should be fine.
    * Added LED labels on the back side
    * Placed a few additio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
    [High Temp Load Cell Toolhead Board.kicad_pcb]
2024-12-31 L1 GND Tweaks
    * Disable all islands in the ground fill zone. This makes it much easier to spot and fix them.
    * Fixed ground island near the ADS1220 reference lines.
    * Fixed ground island at the OR gate near the ADXL345
    [High Temp Load Cell Toolhead Board.kicad_pcb]
2025-01-02 Stencil Registration
    Add holes in the paste layer that match the PCB mounting holes to make registration with the PCB easier.
    [High Temp Load Cell Toolhead Board.kicad_pcb]
2025-01-02 Add Fan LEDs
    * Add LEDs for both fans
    * Reposition Earth to GND Diode to bottom of board for more LED space
    * Re-run the via stitching, this time assuming tented vias can have solder mask on them
    * Solved a problem with zone clearances, set all zone clearances to 0
    [High Temp Load Cell Toolhead Board.kicad_pcb, High Temp Load Cell Toolhead Board.kicad_sch]
2025-01-02 Minor Updates
    * Tweak ground plane min connection size to 0.2mm to improve the areas it can reach
    * Updates to the ADS1220 layout
    * Updates to the decoupling capacitors around the MCU
    [High Temp Load Cell Toolhead Board.kicad_pcb, High Temp Load Cell Toolhead Board.kicad_sch]
2025-01-04 Add USB C Connector
    The commit adds a USB C connector to the back side of the board.
    * This can be used to bench run and test the board without the 24V power supply.
    * Its not designed to be used with the printer is operational, thats what the main connector is for
    * All components are optional and can be omitted
    * Reverse current protection diodes are included to stop current backfeeding into the USB Host in operation
    Other updates:
    * Add 3D Models for the VRM components
    * ADS1220 clock pin should have been tied to ground
    * ADS1220 pad 17 can be connected to AVSS, which is GND in this design
    * Add QR Code with URL to the project, name and version to the back side
    * Add 3 fiducial markers i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
    [High Temp Load Cell Toolhead Board.kicad_pcb, High Temp Load Cell Toolhead Board.kicad_sch]
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2025-01-05 Add Net Class Directives
    This change adds Net Class Directives for 3 types of specialized nets:
    * ADC Signal - a net that may potentially be sensed by an ADC and should be treated as 50 Ohm impedance
    * Digital Signal - a net that will have an oscillating digital signal on it but does not carry any power. This should also be treated as 50 Ohm impedance.
    * Digital Pair - a differential digital pair. This is only used for the USB data pair which is 90 Ohm impedance.
    [High Temp Load Cell Toolhead Board.kicad_pcb, High Temp Load Cell Toolhead Board.kicad_sch]
2025-01-05 Tweaks to U4 Layout
    Rotate u4 90 degrees and move the SPI clock line down to layer 3
    Fix oscillator missing 3d model
    [High Temp Load Cell Toolhead Board.kicad_sch]
2025-01-07 More Targeted GND Paths
    * Fix the TLVM23615RDNR footprint so its pads are plated
    * Add GND vias in locations where via walls exist on layer 1
    * Add GND vias or where a signal transitions across the core material between layer 2 and 3
    * Add some GND vias near power decoupling capacitors
    * Move the ADS1220 ADC signal lines down to layer 32 so they have 100% ground coverage across their length. They were passing under 5V caps and resistors.
    [High Temp Load Cell Toolhead Board.kicad_pcb]
2025-01-08 USB Routing Improvement & Trach Width Change
    * Fix net class assignment of USB lines so they autoroute with the correct rules.
    * Moved the LED CLK line routing so it doesn't cross the USB lines
    * Added a zone of ground fill on layer 3 to cover the USB traces on the back of the board
    * Changes the standard track with to 15mil / 0.381mm. This is what OSH Park say is 50 Ohm in their process.
    Fixup
    Fixup
    [High Temp Load Cell Toolhead Board.kicad_pcb, High Temp Load Cell Toolhead Board.kicad_sch]
2025-01-10 Replace Oscillator Module with Crystal
    * After a bunch of research I've concluded that I cant use the Oscillator Module with Katapult's codebase for the STM32 chips. Added discussion on this to the design doc. Updated design to use a crystal and 2 caps. Exact capacitor values to be calculated later
    * Based on the best advice I can find for decoupling capacitors on the MCU I have moved them to the back side of the board. This allows their footprints to overlap with the MCU itself, reducing the distance from the MCU to the decoupling cap. Also added vias next to the 2 pins on the MCU that are true ground pins. There are other ground connections through GPIO pins but these are high impedance.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
    [High Temp Load Cell Toolhead Board.kicad_pcb, High Temp Load Cell Toolhead Board.kicad_sch]
2025-01-10 Add Via Stitching
    * Re-run via stitching on GND
    * Add capacitor values to crystal caps
    * Update design doc
    * Remove bad assembly document
    [High Temp Load Cell Toolhead Board.kicad_pcb, High Temp Load Cell Toolhead Board.kicad_sch]
2025-01-14 WIP Address community comments
    * Switch to 6 layers and update design rules for new 6 layer process
    * Change fan MOSFETs based on feedback. Drive MOSFETs with level shifter at 5V
    * Add a 5V LDO for the loadcell thats not potentially poisoned by 5V LED noise
    * Delete MAX chip, switch to PT1000
    * Use 2 SPI busses, delete CS lines
    * Move all components to front of board, re-organize layout to fit everything
    * Switch to vertical USBC connector and import model
    The schematic is updated but the routing has not been done
    [High Temp Load Cell Toolhead Board.kicad_pcb, High Temp Load Cell Toolhead Board.kicad_sch]
2025-01-19 Feedback Updates Completed
    * Disconnected unused GPIO pins from ground, use software pulldown instead.
    * Re-rout for OSHPark's 6 layer stackup
    * Shrink reference text to 0.8mmx0.8mm and 5 mil thickness
    [High Temp Load Cell Toolhead Board.kicad_pcb, High Temp Load Cell Toolhead Board.kicad_sch]
2025-01-22 Update 5V Power input
    * Changed 5V USB power to rout in via the main 24V power input. This assumes the buck converter can operate in dropout mode and pass the 5V supply to the LDOs. This avoids potential issues with backfeeding the buck converter.
    * Added a klipper pins file to give meaningful names to pins
    * Added do-not-populate bypass resistors for fans to test tachometer behavior
    [High Temp Load Cell Toolhead Board.kicad_pcb, High Temp Load Cell Toolhead Board.kicad_sch, toolhead_board_pins.cfg]
2025-01-22 Add Thermal Reliefs
    * Enable thermal relief on GND and 3.3V
    * Re-work 5.5V zone to support thermal relief
    * Move vias off of silkscreen
    * Fix vias that are close to pads
    [High Temp Load Cell Toolhead Board.kicad_pcb]
2025-01-23 Add Dotstar Indicator
    This change replaces the indicator LED with a Dotstar RGB LED. This allows various conditions to be indicated at the toolhead via colors, brightness and blinking.
    * Fixed missing guard ring on layers 4 and 5.
    [High Temp Load Cell Toolhead Board.kicad_pcb, High Temp Load Cell Toolhead Board.kicad_sch]
2025-01-23 Minor Track Tweaking
    Just making sure tracks clear vias and everything looks manufacturable.
    [High Temp Load Cell Toolhead Board.kicad_pcb]
2025-01-24 Move Filament Switch & Heatbreak Thermistor to ADC Inputs
    * Move Filament switch line from PA15 to PA7
    * Move Heatberak Thermistor from PB1 to PA6 (PB1 is Boot1)
    * Re-routed Filament switch line on the back side of the PCB
    * Edited pin assignments for thermistors to make routing cleaner
    * Updated pins file to reflect changes
    * Renamed Neopixel port to Dotstar.
    [High Temp Load Cell Toolhead Board.kicad_pcb, High Temp Load Cell Toolhead Board.kicad_sch, toolhead_board_pins.cfg]
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
